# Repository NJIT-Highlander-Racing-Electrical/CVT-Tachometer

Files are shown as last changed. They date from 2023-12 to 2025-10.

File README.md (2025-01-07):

 # CVT-Tachometer

A subsystem that measures the RPM of the primary and secondary on the CVT. This subsystem also has a temperature sensor to detect if the CVT is overheating.

## 2024-2025 Design Goals

* Everything last year seemed to work well, but a few improvements to the existing system could be made:
  * Software
       * Improve program to do more analog reads and spend less time processing data
          * This may involve constants that are only calculated once during setup, faster math functions, fewer delays, etc
       * Use the analog reads for IR sensors on both ADC1 and ADC2 to prevent any issues. 
  * Sensor Enclosures
       * the sensor housings should be made out of something other than PLA
       * they should be able to fit custom PCBs with connectors
       * the hood around the emitter and receiver should be enlarged to prevent anything else from reflecting other than what is directly in front
  * PCBs for sensors
       * the wiring from the sensors to the main electronics housing were tough to do
       * A small PCB for the electronics would be nicer than hand soldering wires
       * A connector would also be good so that they can be removed/swapped easily
            * Maybe 1x4 or 1x5 or 1x6 JST depending on how many conductors we need going to each board
  * Additional TMP36 Sensor
      * Another TMP36 temperature sensor can be added so that there is only one version of the sensor PCB, and we get a better idea of the temperature gradient within the CVT case (primary vs secondary).
  * Additional Note
     * On the IR receiver output, have it split to two GPIO. One leg has a potentiometer (0-10k?) between the output and the GPIO for finding the optimal resistance. Also make sure it has a small series resistor to prevent resistance from dropping completely to zero. The other GPIO has a fixed resistor that can be added after the fact that will be used in the long term. 

## Hardware Components:

* IR Sensors that point at primary and secondary.
- These can detect when a white stripe on the CVT passes by (one revolution)
* Microcontroller to convert the number of revolutions per second into an RPM value for dashboard and DAS (via CAN-Bus)
  - Uses ESP32 and TJA1051T CAN-Bus transceiver
* TMP36 Temperature Sensor to look at ambient temperature in the CVT case
- Sends a bit via CAN-Bus to turn on an overheating status LED on the dashboard

 ## Notes

 * Super-Bright IR LEDs support an output current of 100mA with a forward voltage of 1.6V. This means a voltage drop of 5V-1.6V = 3.4V across the 1W resistor. To achieve a current of roughly 75mA, we are using a 47 ohm resistor
    * 5V -> IR LED -> Resistor -> Ground
 * Using standard infrared photodiodes, we can simply power the IR leds without needing a 38kHz pulse rate
    * 5V -> IR Diode -> Resistor -> Ground (sample signal between diode and resistor voltage divider)
 * Temperature sensor is TMP36
    * 5V - > TMP36 VCC, GND -> TMP 36 GND, VOUT -> GPIO
 * Connections from the LEDs/sensors to the main body should be sealed/waterproof
 * The holes in the CVT case should be 20mm
 * The infrared diode appears to act like a variable resistor, but voltage polarity must be + on cathode (short negative leg) and - on anode (short positive leg)

 * The software utilizes the dual core functionality of the ESP32
   * Core 1 reads primaryRPM and deals with CAN-Bus communication
      * It is very important that all other processing is kept to a minimum to ensure primaryRPM is accurately read
   * Core 0 solely reads secondaryRPM

### Previous Issues 
 * One issue noticed during the testing phase was that the analog sensor readings were constantly peaking (4095). The resistor divider for the IR receivers needed to be adjusted to roughly 2700 ohms
 * It looked like the analog readings were having issues at comp too. It was either 0-3 ish mph or 41
     * This has been solved on 9/18/24 with dynamically adjusting analog thresholds
 * Analog reads are not ideal for this type of data acquisition. Fast readings are needed, and there should be no margin for error about whether a reading falls within a range
 * Digital readings with a hall sensor, engine spark plug with octocoupler, or some other digital signal could be implemented 

## Electrical Wiring Notes

### Pins to sensor modules

* Pin 1: +5V
* Pin 2: GND
* Pin 3: TMP36 Output
* Pin 4: IR Emitter Return Line
* Pin 5: IR Receiver Return Line

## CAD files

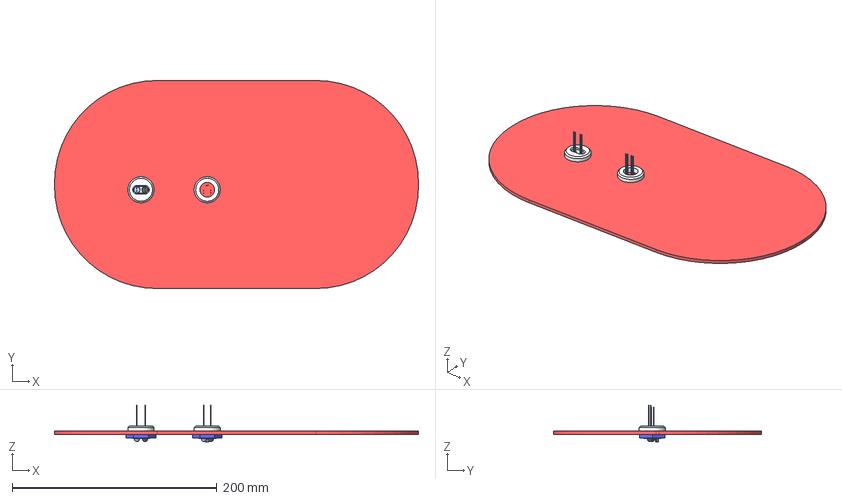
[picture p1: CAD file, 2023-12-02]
3D Models/CVT Infrared Sensors Full Model.step
355.6 x 203.2 x 35.7 mm
5mm LED v1 x 2
5mm LED v1 (1) x 2
TO92 Transistor TMP36 Temperature Sensor Package

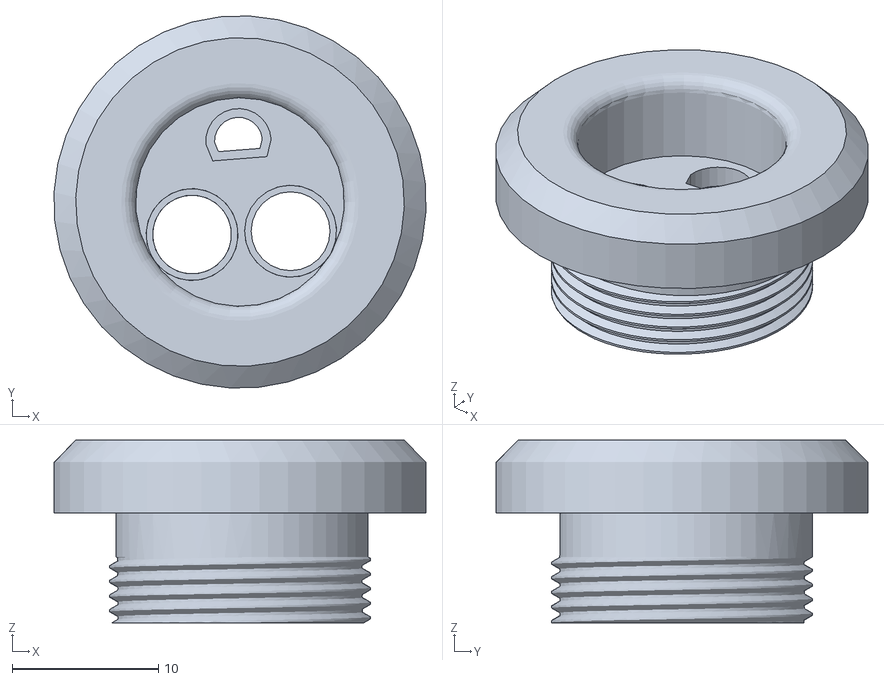
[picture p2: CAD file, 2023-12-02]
3D Models/CVT Infrared Sensors Main Body (With Temperature Sensor).stl
25.5 x 25.5 x 12.5

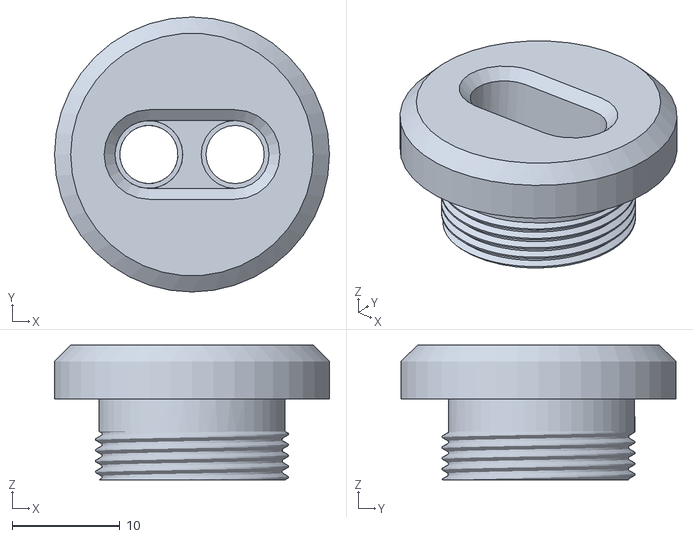
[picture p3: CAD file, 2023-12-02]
3D Models/CVT Infrared Sensors Main Body (No Temperature Sensor).stl
25.5 x 25.5 x 12.5

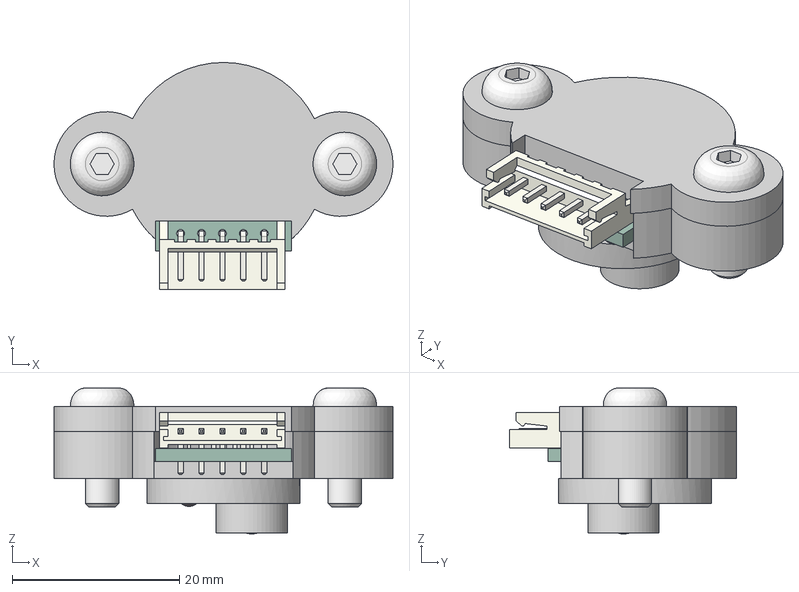
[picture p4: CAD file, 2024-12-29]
3D Models/CVT Sensor Module Enclosures v5.step
40.5 x 27.1 x 17.4 mm
JST_S5B_EH
LED_D3.0mm_IRBlack_1
TO-92_Inline_Narrow
LED_D5.0mm_IRGrey_1
SensorPCB_PCB
VITE_TESTA_BOMBATA_ESAGONO_INCASSATO x 2

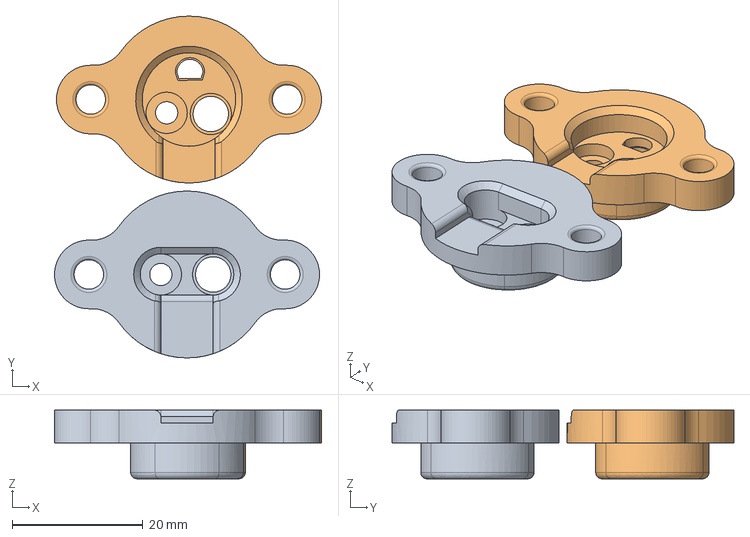
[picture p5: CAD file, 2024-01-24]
3D Models/CVT Infrared Sensor Mounts.step
40.8 x 52.2 x 10.5 mm

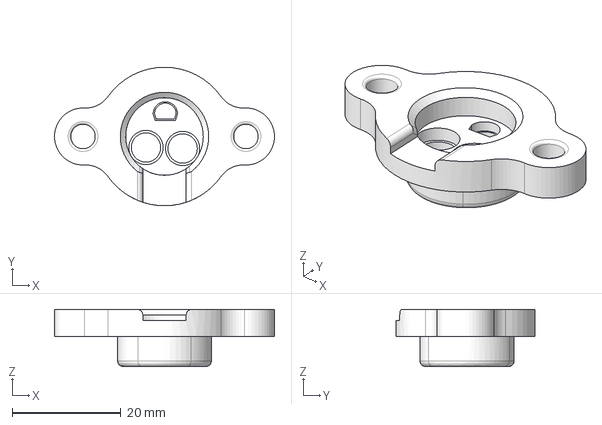
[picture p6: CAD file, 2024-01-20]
3D Models/Sensor Mount with Temperature.step
40.5 x 25.5 x 10.5 mm

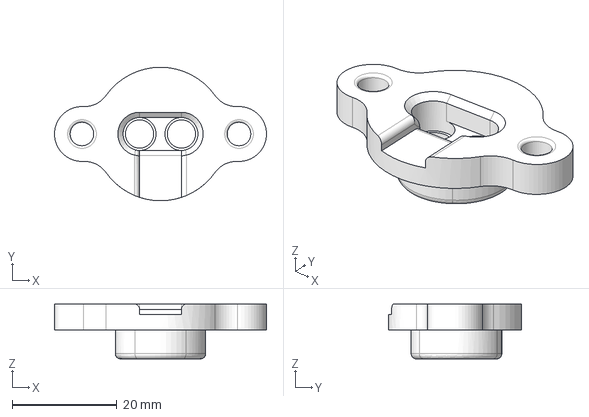
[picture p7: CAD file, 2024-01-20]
3D Models/Sensor Mount No Temperature.step
40.5 x 25.5 x 10.5 mm

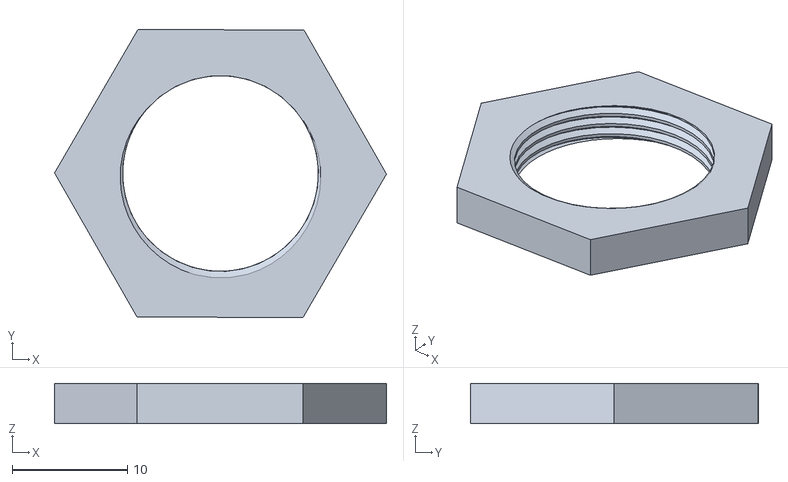
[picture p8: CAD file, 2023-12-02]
3D Models/CVT Infrared Sensors Nut.stl
28.9 x 25.0 x 3.50

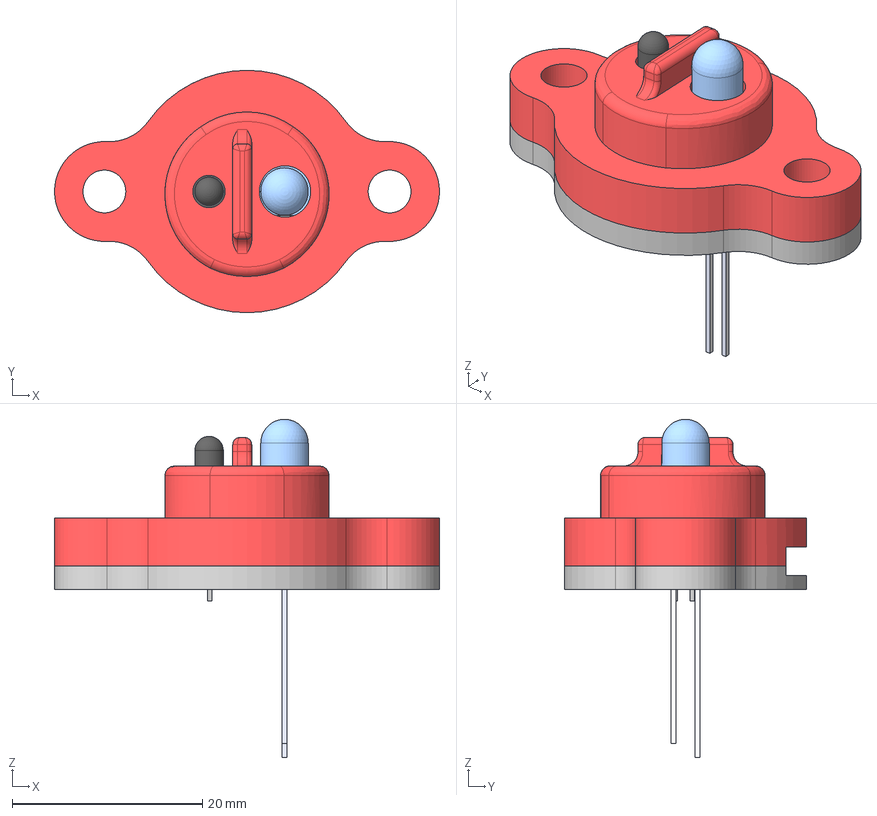
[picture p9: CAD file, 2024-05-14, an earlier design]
2023-2024 Archive/3D Models/CVT Infrared Sensor (no temperature).step
40.5 x 25.5 x 35.6 mm
5mm LED v1
led_energy
led_pin.1.1.1
led_pin.2.1

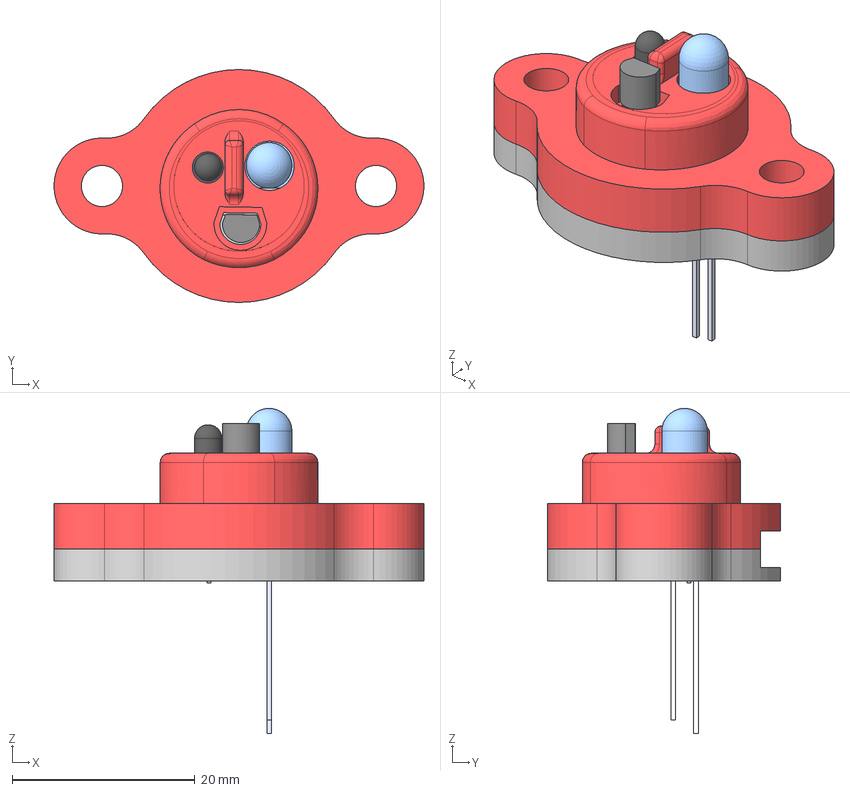
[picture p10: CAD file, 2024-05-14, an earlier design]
2023-2024 Archive/3D Models/CVT Infrared Sensors (with temperature).step
40.5 x 25.5 x 35.6 mm
TO92 Transistor TMP36 Temperature Sensor Package
5mm LED v1
led_energy
led_pin.1.1.1
led_pin.2.1

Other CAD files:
3D Models/Alternative Designs/CVTMain v2.step
2023-2024 Archive/3D Models/OldDesigns/CVT Infrared Sensors Full Model.step
2023-2024 Archive/3D Models/OldDesigns/Sensor Mount No Temperature.step
2023-2024 Archive/3D Models/OldDesigns/Sensor Mount with Temperature.step
2023-2024 Archive/3D Models/OldDesigns/CVT Infrared Sensor Mounts.step
3D Models/CVT Sensor Module Enclosures.f3z

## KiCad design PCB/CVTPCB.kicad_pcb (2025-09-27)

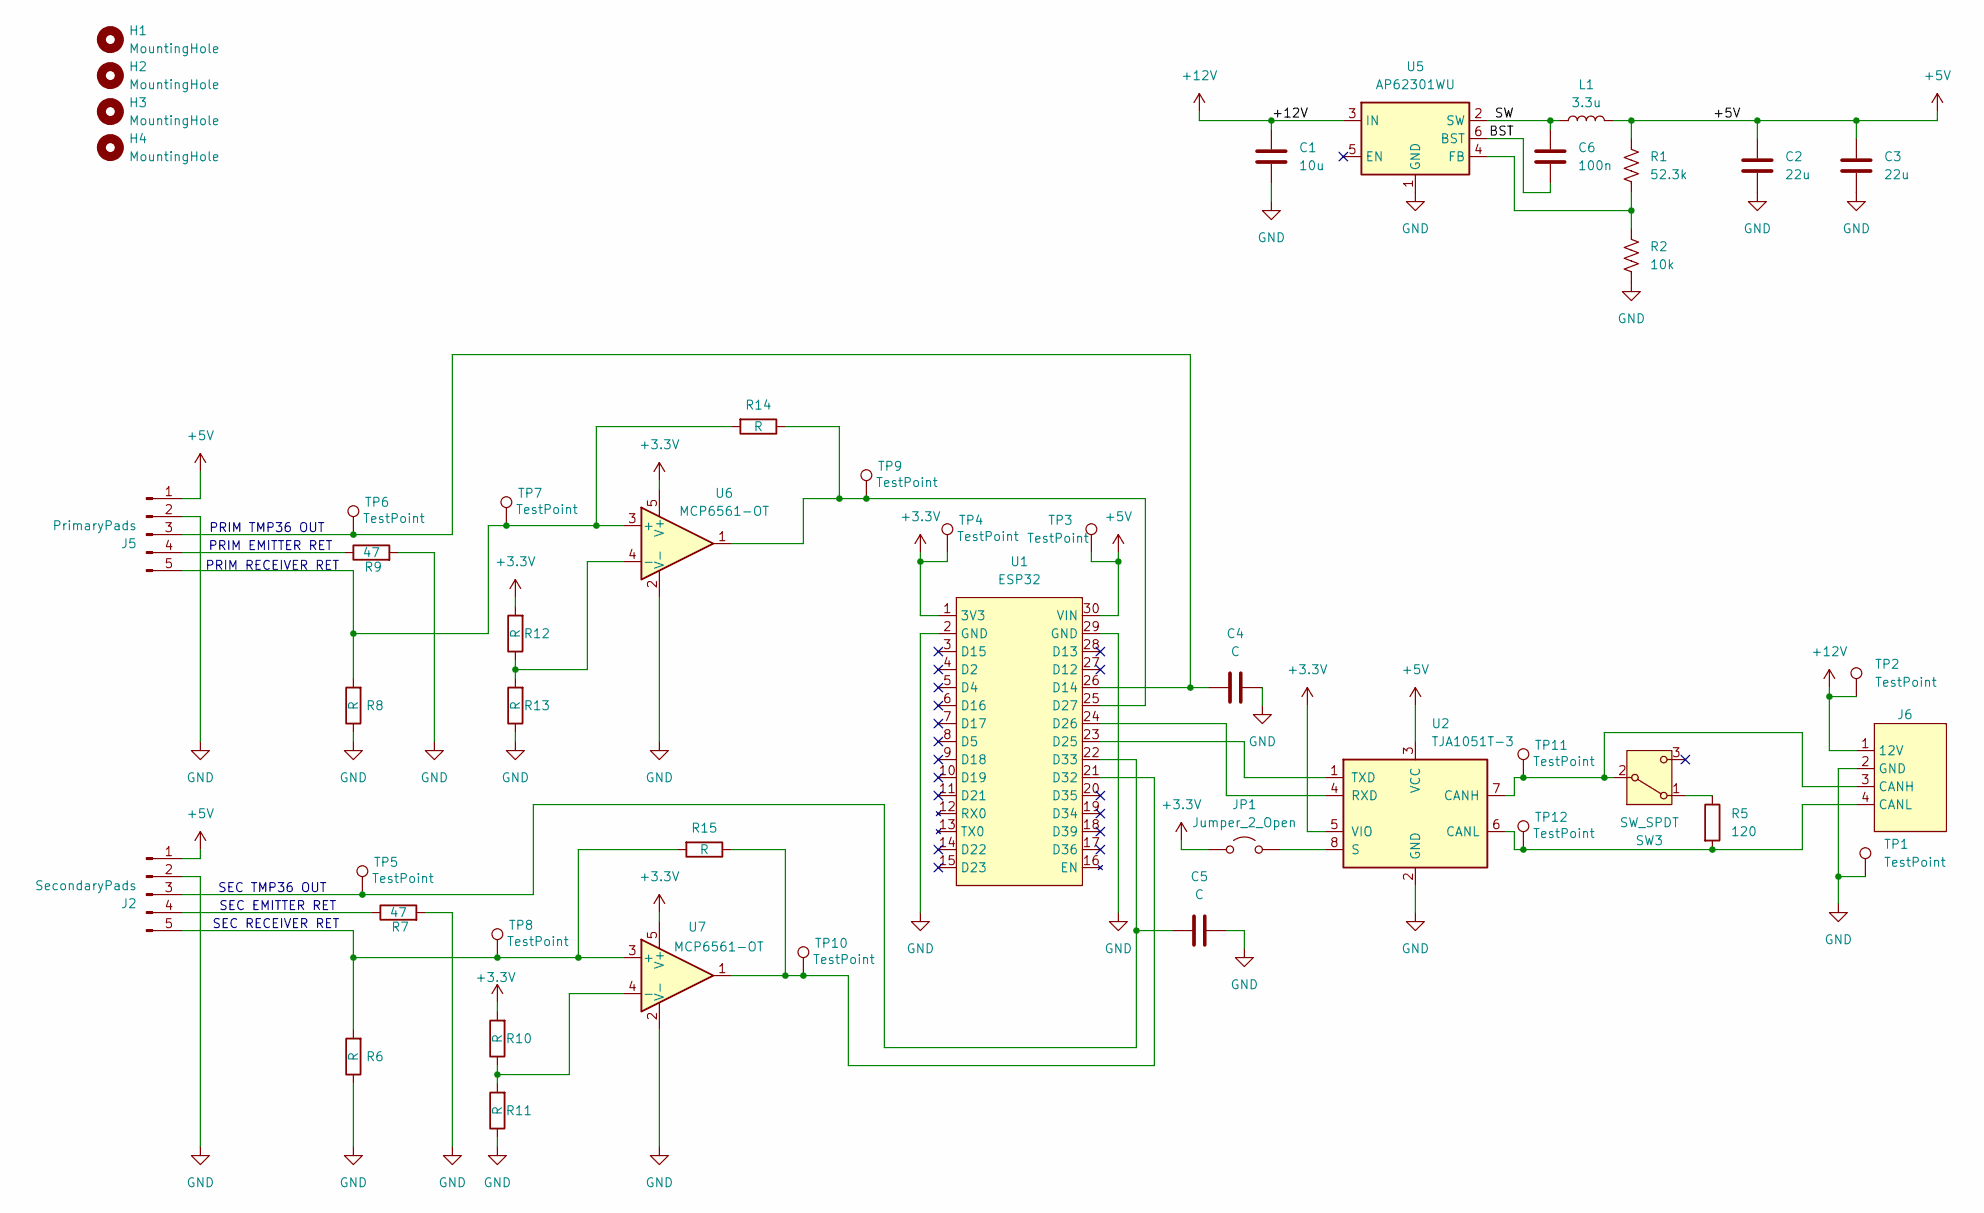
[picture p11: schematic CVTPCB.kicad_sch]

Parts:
C1: 10u; C_0805_2012Metric_Pad1.18x1.45mm_HandSolder
C2, C3: 22u; C_0603_1608Metric_Pad1.08x0.95mm_HandSolder
C4, C5: C; C_0805_2012Metric_Pad1.18x1.45mm_HandSolder
C6: 100n; C_0402_1005Metric_Pad0.74x0.62mm_HandSolder
H1, H2, H3, H4: MountingHole; MountingHole_4.3mm_M4
J2: SecondaryPads; Temp_IR_5_Pad_Combo
J5: PrimaryPads; Temp_IR_5_Pad_Combo
J6: Aviation Plug Pads
JP1: Jumper_2_Open; SolderJumper-2_P1.3mm_Open_Pad1.0x1.5mm
L1: 3.3u; L_Taiyo-Yuden_NR-50xx
R1: 52.3k; R_0402_1005Metric
R2: 10k; R_0402_1005Metric
R5: 120; R_1206_3216Metric_Pad1.30x1.75mm_HandSolder
R6, R8, R10, R11, R12, R13, R14, R15: R; R_1206_3216Metric_Pad1.30x1.75mm_HandSolder
R7, R9: 47; R_Axial_DIN0411_L9.9mm_D3.6mm_P12.70mm_Horizontal
SW3: SW_SPDT; SW_SPDT_CK_JS102011SAQN
TP1, TP2, TP3, TP4, TP5, TP6, TP7, TP8, TP9, TP10, TP11, TP12: TestPoint; TestPoint_THTPad_D3.0mm_Drill1.5mm
U1: ESP32
U2: TJA1051T-3; SOIC-8_3.9x4.9mm_P1.27mm
U5: AP62301WU; TSOT-23-6
U6, U7: MCP6561-OT; SOT-23-5

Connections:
+3.3V: JP1.1 (A), R10.2, R12.2, TP4.1, U1.1 (3V3), U2.5 (VIO), U6.5 (V+), U7.5 (V+)
+5V: C2.1, C3.1, J2.1, J5.1, L1.2, R1.1, TP3.1, U1.30 (VIN), U2.3 (VCC)
+12V: C1.1, J6.1 (12V), TP2.1, U5.3 (IN)
/BST: C6.2, U5.6 (BST)
/SW: C6.1, L1.1, U5.2 (SW)
GND: C1.2, C2.2, C3.2, C4.2, C5.2, J2.2, J5.2, J6.2 (GND), R2.2, R6.1, R7.2, R8.1, R9.2, R11.1, R13.1, TP1.1, U1.2 (GND), U1.29 (GND), U2.2 (GND), U5.1 (GND), U6.2 (V-), U7.2 (V-)
unnamed: C5.1, J2.3, TP5.1, U1.22 (D33)
unnamed: J2.4, R7.1
unnamed: J2.5, R6.2, R15.2, TP8.1, U7.3 (+)
unnamed: C4.1, J5.3, TP6.1, U1.26 (D14)
unnamed: J5.4, R9.1
unnamed: J5.5, R8.2, R14.2, TP7.1, U6.3 (+)
unnamed: J6.3 (CANH), SW3.2 (B), TP11.1, U2.7 (CANH)
unnamed: J6.4 (CANL), R5.2, TP12.1, U2.6 (CANL)
unnamed: JP1.2 (B), U2.8 (S)
unnamed: R5.1, SW3.1 (A)
unnamed: U1.23 (D25), U2.1 (TXD)
unnamed: U1.24 (D26), U2.4 (RXD)
unnamed: R14.1, TP9.1, U1.25 (D27), U6.1
unnamed: R15.1, TP10.1, U1.21 (D32), U7.1
unnamed: R1.2, R2.1, U5.4 (FB)
unnamed: R12.1, R13.2, U6.4 (-)
unnamed: R10.1, R11.2, U7.4 (-)

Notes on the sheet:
PRIM TMP36 OUT
SEC RECEIVER RET
SEC EMITTER RET
PRIM EMITTER RET
PRIM RECEIVER RET
SEC TMP36 OUT

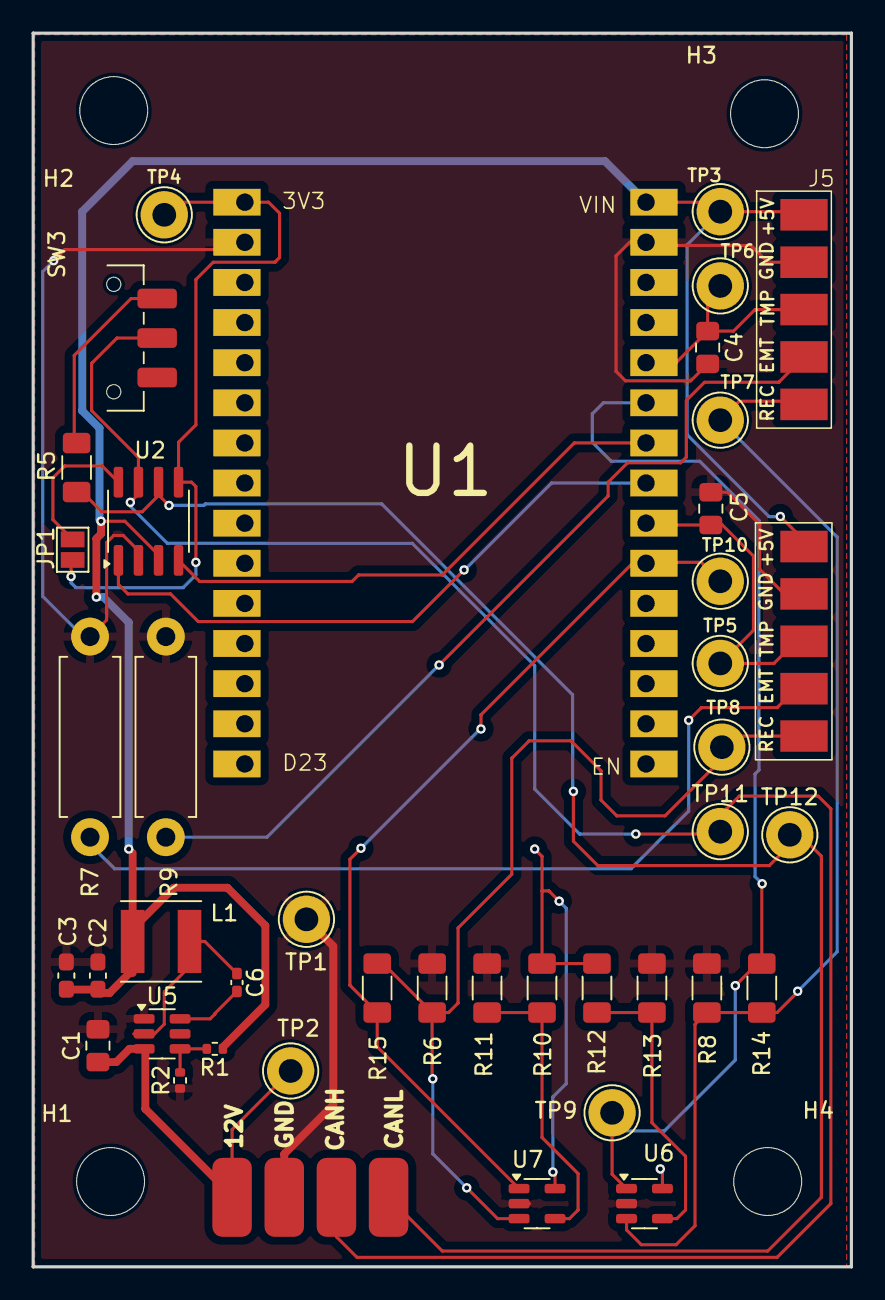
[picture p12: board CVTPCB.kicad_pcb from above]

Board: 2 copper layers, 51.8 x 78.1 mm, 46 parts (0 on the bottom side), 23 nets.

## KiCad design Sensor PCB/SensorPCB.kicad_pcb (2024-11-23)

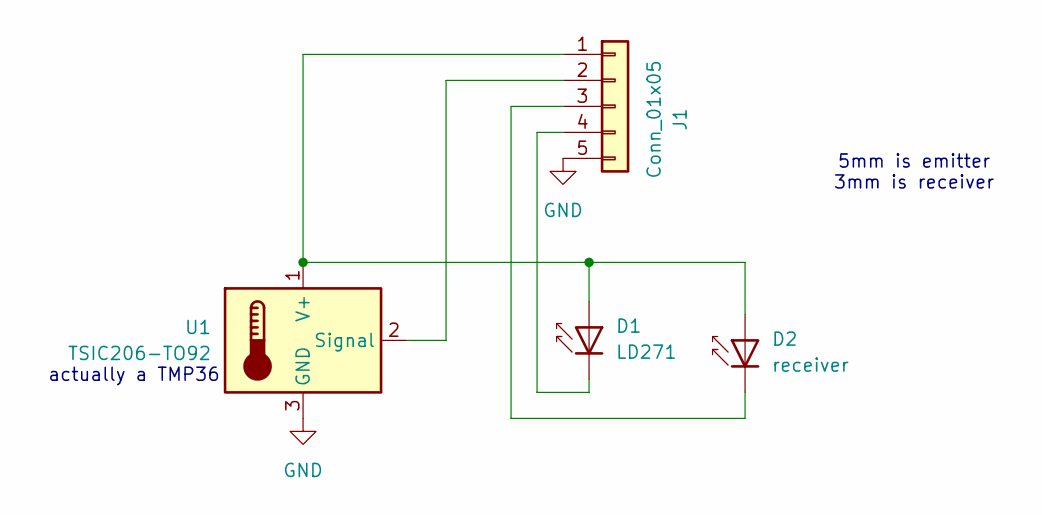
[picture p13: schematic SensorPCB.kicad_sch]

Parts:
D1: LD271; LED_D5.0mm_IRGrey
D2: receiver; LED_D3.0mm_IRBlack
J1: Conn_01x05; JST_EH_B5B-EH-A_1x05_P2.50mm_Vertical
U1: TSIC206-TO92; TO-92_Inline

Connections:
GND: J1.5, U1.3 (GND)
unnamed: D1.2 (A), D2.2 (A), J1.1, U1.1 (V+)
unnamed: D1.1 (K), J1.4
unnamed: D2.1 (K), J1.3
unnamed: J1.2, U1.2 (Signal)

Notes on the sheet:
5mm is emitter 3mm is receiver
actually a TMP36

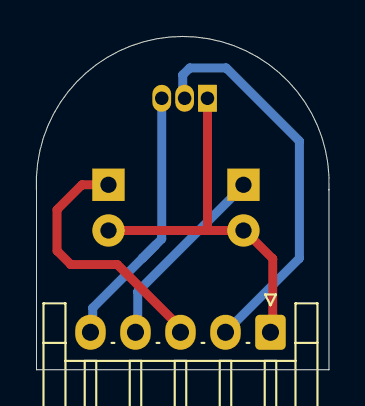
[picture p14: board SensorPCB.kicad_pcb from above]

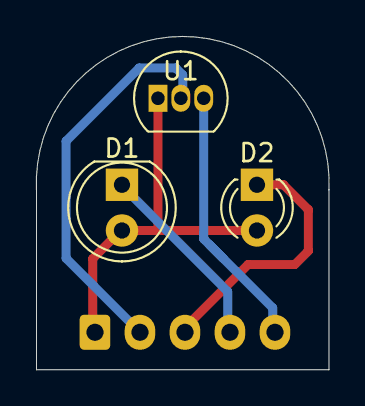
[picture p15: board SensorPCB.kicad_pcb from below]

Board: 2 copper layers, 16.3 x 18.5 mm, 4 parts (3 on the bottom side), 5 nets.

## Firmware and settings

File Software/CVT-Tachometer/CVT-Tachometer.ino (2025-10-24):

/*
* CVT Tachometer with IR sensors and temperature monitoring
* Fixed timing issues, race conditions, and improved filtering
*/

#include "BajaCAN.h"
#include <Wire.h>

// Set DEBUG to false for final program
#define DEBUG true

#define DEBUG_SERIAL \
  if (DEBUG) Serial

#define PRIMARY_IR 32    // Primary Comparator Output
#define PRIMARY_TEMP 33  // Primary TMP36 Sensor pin

#define SECONDARY_IR 27    // Secondary Comparator Output
#define SECONDARY_TEMP 14  // Secondary TMP36 Sensor pin

// MLX90614 I2C Configuration
#define MLX90614_I2C_ADDR 0x5A
#define MLX90614_OBJECT_TEMP 0x07
#define I2C_SDA 21
#define I2C_SCL 22

// USER-DEFINED PARAMETERS
const int debugPrintInterval = 100;
const int tempUpdateFrequency = 500;
const int numPrimaryTargets = 8;
const int numSecondaryTargets = 3;

// Timeout if no pulse in 1 second (1,000,000 microseconds)
const unsigned long timeoutThreshold = 1000000;

// Debounce time - adjusted for realistic RPM ranges
// Primary: 8 targets, max ~4000 RPM = 533 pulses/sec = 1875us between pulses
// Secondary: 3 targets, max ~4000 RPM = 200 pulses/sec = 5000us between pulses
// Set debounce to 1500us to allow fast speeds while rejecting noise
const unsigned long debounceTimeMicros = 1500;

// Maximum reasonable RPM to filter out noise spikes
const int MAX_PRIMARY_RPM = 5000;
const int MAX_SECONDARY_RPM = 5000;

// END USER PARAMETERS

// Serial Print timing
int lastPrintTime = 0;

// Primary timing variables (all volatile for ISR safety)
volatile unsigned long currentPrimaryReadTime = 0;
volatile unsigned long lastPrimaryReadTime = 0;
volatile bool primaryUpdateFlag = false;

// Secondary timing variables
volatile unsigned long currentSecondaryReadTime = 0;
volatile unsigned long lastSecondaryReadTime = 0;
volatile bool secondaryUpdateFlag = false;

// Temperature timing
unsigned long lastPrimTempReadTime = 0;
unsigned long lastSecTempReadTime = 0;
unsigned long lastBeltTempReadTime = 0;

// State flags
bool primaryIsFirstReading = true;
bool secondaryIsFirstReading = true;
bool primaryIgnoreNext = false;
bool secondaryIgnoreNext = false;

// Moving average filter (median filter for better spike rejection)
const int RPM_FILTER_SIZE = 5;
int primaryRPMBuffer[RPM_FILTER_SIZE] = {0};
int secondaryRPMBuffer[RPM_FILTER_SIZE] = {0};
int primaryBufferIndex = 0;
int secondaryBufferIndex = 0;
int primaryBufferCount = 0;  // Track how many samples we have
int secondaryBufferCount = 0;

// Function Prototypes
void primaryISR();
void secondaryISR();
void readPrimaryTemp();
void readSecondaryTemp();
void readBeltTemp();
void checkPrimaryTimeout();
void checkSecondaryTimeout();
int calculateMedianRPM(int* buffer, int size);
void printData();

void setup() {
  Serial.begin(460800);
  delay(100);

  // Initialize I2C for MLX90614
  Wire.begin(I2C_SDA, I2C_SCL);
  
  // Initialize CAN - send every 25ms (40Hz)
  setupCAN(CVT, 25);

  // Configure pins
  pinMode(PRIMARY_IR, INPUT);
  pinMode(PRIMARY_TEMP, INPUT);
  pinMode(SECONDARY_IR, INPUT);
  pinMode(SECONDARY_TEMP, INPUT);

  // Initialize timing to current time
  unsigned long now = micros();
  currentPrimaryReadTime = now;
  lastPrimaryReadTime = now;
  currentSecondaryReadTime = now;
  lastSecondaryReadTime = now;

  // Attach interrupts on rising edge
  attachInterrupt(digitalPinToInterrupt(PRIMARY_IR), primaryISR, RISING);
  attachInterrupt(digitalPinToInterrupt(SECONDARY_IR), secondaryISR, RISING);

  DEBUG_SERIAL.println("CVT Tachometer Initialized");
  DEBUG_SERIAL.print("Primary targets: ");
  DEBUG_SERIAL.println(numPrimaryTargets);
  DEBUG_SERIAL.print("Secondary targets: ");
  DEBUG_SERIAL.println(numSecondaryTargets);
  DEBUG_SERIAL.print("Debounce time (us): ");
  DEBUG_SERIAL.println(debounceTimeMicros);
}

void loop() {
  // Check for timeouts
  checkPrimaryTimeout();
  checkSecondaryTimeout();

  // Process primary RPM calculation
  if (primaryUpdateFlag) {
    // Capture timing atomically
    noInterrupts();
    unsigned long capturedCurrent = currentPrimaryReadTime;
    unsigned long capturedLast = lastPrimaryReadTime;
    primaryUpdateFlag = false;
    interrupts();

    // Skip first reading - need two points to calculate
    if (primaryIsFirstReading) {
      noInterrupts();
      lastPrimaryReadTime = capturedCurrent;
      interrupts();
      primaryIsFirstReading = false;
      primaryIgnoreNext = false;
      DEBUG_SERIAL.println("Primary: First reading captured");
    }
    // If recovering from timeout, re-establish baseline
    else if (primaryIgnoreNext) {
      noInterrupts();
      lastPrimaryReadTime = capturedCurrent;
      interrupts();
      primaryIgnoreNext = false;
      DEBUG_SERIAL.println("Primary: Baseline re-established after timeout");
    }
    // Normal calculation
    else {
      unsigned long elapsed = capturedCurrent - capturedLast;
      
      if (elapsed > 0) {
        // Calculate RPM: (60,000,000 microseconds/min) / elapsed / targets
        int calculatedRPM = (60000000.0 / elapsed) / numPrimaryTargets;

        // Sanity check
        if (calculatedRPM > 0 && calculatedRPM < MAX_PRIMARY_RPM) {
          // Add to buffer
          primaryRPMBuffer[primaryBufferIndex] = calculatedRPM;
          primaryBufferIndex = (primaryBufferIndex + 1) % RPM_FILTER_SIZE;
          if (primaryBufferCount < RPM_FILTER_SIZE) {
            primaryBufferCount++;
          }
          
          // Calculate filtered value
          primaryRPM = calculateMedianRPM(primaryRPMBuffer, primaryBufferCount);
          
          // Update last reading time atomically
          noInterrupts();
          lastPrimaryReadTime = capturedCurrent;
          interrupts();
        } else {
          DEBUG_SERIAL.print("Primary RPM rejected: ");
          DEBUG_SERIAL.println(calculatedRPM);
        }
      }
    }
  }

  // Process secondary RPM calculation
  if (secondaryUpdateFlag) {
    // Capture timing atomically
    noInterrupts();
    unsigned long capturedCurrent = currentSecondaryReadTime;
    unsigned long capturedLast = lastSecondaryReadTime;
    secondaryUpdateFlag = false;
    interrupts();

    // Skip first reading - need two points to calculate
    if (secondaryIsFirstReading) {
      noInterrupts();
      lastSecondaryReadTime = capturedCurrent;
      interrupts();
      secondaryIsFirstReading = false;
      secondaryIgnoreNext = false;
      DEBUG_SERIAL.println("Secondary: First reading captured");
    }
    // If recovering from timeout, re-establish baseline
    else if (secondaryIgnoreNext) {
      noInterrupts();
      lastSecondaryReadTime = capturedCurrent;
      interrupts();
      secondaryIgnoreNext = false;
      DEBUG_SERIAL.println("Secondary: Baseline re-established after timeout");
    }
    // Normal calculation
    else {
      unsigned long elapsed = capturedCurrent - capturedLast;
      
      if (elapsed > 0) {
        // Calculate RPM
        int calculatedRPM = (60000000.0 / elapsed) / numSecondaryTargets;

        // Sanity check
        if (calculatedRPM > 0 && calculatedRPM < MAX_SECONDARY_RPM) {
          // Add to buffer
          secondaryRPMBuffer[secondaryBufferIndex] = calculatedRPM;
          secondaryBufferIndex = (secondaryBufferIndex + 1) % RPM_FILTER_SIZE;
          if (secondaryBufferCount < RPM_FILTER_SIZE) {
            secondaryBufferCount++;
          }
          
          // Calculate filtered value
          secondaryRPM = calculateMedianRPM(secondaryRPMBuffer, secondaryBufferCount);
          
          // Update last reading time atomically
          noInterrupts();
          lastSecondaryReadTime = capturedCurrent;
          interrupts();
        } else {
          DEBUG_SERIAL.print("Secondary RPM rejected: ");
          DEBUG_SERIAL.println(calculatedRPM);
        }
      }
    }
  }

  // Read temperatures
  readPrimaryTemp();
  readSecondaryTemp();
  readBeltTemp();

  // Print debug data
  if (DEBUG && (millis() - lastPrintTime) > debugPrintInterval) {
    lastPrintTime = millis();
    printData();
  }
}

/*
 * FUNCTION DEFINITIONS
 */

void primaryISR() {
  unsigned long now = micros();
  
  // Debounce: ignore pulses too close together
  unsigned long timeSinceLast = now - currentPrimaryReadTime;
  if (timeSinceLast < debounceTimeMicros) {
    return;  // Noise/bounce, ignore
  }
  
  // Update timing
  lastPrimaryReadTime = currentPrimaryReadTime;
  currentPrimaryReadTime = now;
  primaryUpdateFlag = true;
}

void secondaryISR() {
  unsigned long now = micros();
  
  // Debounce: ignore pulses too close together
  unsigned long timeSinceLast = now - currentSecondaryReadTime;
  if (timeSinceLast < debounceTimeMicros) {
    return;  // Noise/bounce, ignore
  }
  
  // Update timing
  lastSecondaryReadTime = currentSecondaryReadTime;
  currentSecondaryReadTime = now;
  secondaryUpdateFlag = true;
}

void checkPrimaryTimeout() {
  unsigned long currentTime = micros();
  unsigned long timeSinceLastPulse = currentTime - currentPrimaryReadTime;
  
  if (timeSinceLastPulse > timeoutThreshold) {
    if (primaryRPM != 0) {  // Only update if not already zero
      primaryRPM = 0;
      primaryIgnoreNext = true;  // Ignore next pulse to re-establish baseline
      
      // Clear the buffer
      for (int i = 0; i < RPM_FILTER_SIZE; i++) {
        primaryRPMBuffer[i] = 0;
      }
      primaryBufferCount = 0;
      primaryBufferIndex = 0;
      
      DEBUG_SERIAL.println("Primary timeout - RPM set to 0");
    }
  }
}

void checkSecondaryTimeout() {
  unsigned long currentTime = micros();
  unsigned long timeSinceLastPulse = currentTime - currentSecondaryReadTime;
  
  if (timeSinceLastPulse > timeoutThreshold) {
    if (secondaryRPM != 0) {  // Only update if not already zero
      secondaryRPM = 0;
      secondaryIgnoreNext = true;  // Ignore next pulse to re-establish baseline
      
      // Clear the buffer
      for (int i = 0; i < RPM_FILTER_SIZE; i++) {
        secondaryRPMBuffer[i] = 0;
      }
      secondaryBufferCount = 0;
      secondaryBufferIndex = 0;
      
      DEBUG_SERIAL.println("Secondary timeout - RPM set to 0");
    }
  }
}

int calculateMedianRPM(int* buffer, int count) {
  if (count == 0) return 0;
  
  // Create temporary array for sorting
  int sortedBuffer[RPM_FILTER_SIZE];
  memcpy(sortedBuffer, buffer, count * sizeof(int));
  
  // Bubble sort
  for (int i = 0; i < count - 1; i++) {
    for (int j = 0; j < count - i - 1; j++) {
      if (sortedBuffer[j] > sortedBuffer[j + 1]) {
        int temp = sortedBuffer[j];
        sortedBuffer[j] = sortedBuffer[j + 1];
        sortedBuffer[j + 1] = temp;
      }
    }
  }
  
  // Return median value
  return sortedBuffer[count / 2];
}

void readPrimaryTemp() {
  if ((millis() - lastPrimTempReadTime) > tempUpdateFrequency) {
    long total = 0;

    // Average 10 readings
    for (int i = 0; i < 10; i++) {
      total += analogRead(PRIMARY_TEMP);
    }

    int primTempReading = total / 10;
    float primTempVoltage = (float)primTempReading * 3.3 / 4095.0;
    float primTempC = (primTempVoltage - 0.5) * 100;
    primaryTemperature = (primTempC * 9.0 / 5.0) + 32.0;

    lastPrimTempReadTime = millis();
  }
}

void readSecondaryTemp() {
  if ((millis() - lastSecTempReadTime) > tempUpdateFrequency) {
    long total = 0;

    // Average 10 readings
    for (int i = 0; i < 10; i++) {
      total += analogRead(SECONDARY_TEMP);
    }

    int secTempReading = total / 10;
    float secTempVoltage = (float)secTempReading * 3.3 / 4095.0;
    float secTempC = (secTempVoltage - 0.5) * 100;
    secondaryTemperature = (secTempC * 9.0 / 5.0) + 32.0;

    lastSecTempReadTime = millis();
  }
}

void readBeltTemp() {
  if ((millis() - lastBeltTempReadTime) > tempUpdateFrequency) {
    Wire.beginTransmission(MLX90614_I2C_ADDR);
    Wire.write(MLX90614_OBJECT_TEMP);
    
    if (Wire.endTransmission(false) == 0) {
      Wire.requestFrom(MLX90614_I2C_ADDR, 3);
      
      if (Wire.available() >= 2) {
        uint8_t tempLow = Wire.read();
        uint8_t tempHigh = Wire.read();
        Wire.read(); // Discard PEC byte
        
        uint16_t tempRaw = (tempHigh << 8) | tempLow;
        float tempK = tempRaw * 0.02;
        float tempC = tempK - 273.15;
        float tempF = (tempC * 9.0 / 5.0) + 32.0;
        
        beltTemperature = (int)tempF;
      }
    }
    
    lastBeltTempReadTime = millis();
  }
}

void printData() {
  DEBUG_SERIAL.print("pRpm:");
  DEBUG_SERIAL.print(primaryRPM);
  DEBUG_SERIAL.print(", pTemp:");
  DEBUG_SERIAL.print(primaryTemperature);
  DEBUG_SERIAL.print(", sRpm:");
  DEBUG_SERIAL.print(secondaryRPM);
  DEBUG_SERIAL.print(", sTemp:");
  DEBUG_SERIAL.print(secondaryTemperature);
  DEBUG_SERIAL.print(", beltTemp:");
  DEBUG_SERIAL.println(beltTemperature);
}

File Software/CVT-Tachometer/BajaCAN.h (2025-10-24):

/*********************************************************************************
*
*   BajaCAN.h  -- Version 2.2.2 - Native ESP32 CAN Driver
*
*   The goal of this BajaCAN header/driver is to enable all subsystems throughout
*   the vehicle to use the same variables, data types, and functions. That way,
*   any changes made to the CAN bus system can easily be applied to each subsystem
*   by simply updating the version of this file.

*
*     This driver serves several functions:
*

*     *** CAN Setup/Initialization ***
*
*     This CAN driver declares all of the variables that will be used in
*     CAN transmissions. That way, there is no confusion as to what data packet
*     a variable name refers to. In addition, declaring the variables in the CAN
*     header file allows for each variable to have the same data type. If one
*     subsystem were to use a float for an RPM value while another uses an integer,
*     there is a chance we could run into issues.
*
*     Before using CAN, several initialization steps must be taken. Since this must
*     happen during the setup() of the main code, there is a function named
*     setupCAN() that can be called in the setup() portion to execute all CAN setup.
*     Ideally, all subsystems will use the same pair of GPIO for CAN that do not
*     have any special functions. However, if setup does differ between subsystems,
*     setupCAN() has optional arguments for baud rate, GPIO, send frequency, etc.
*     The only argument that must be passed into setupCAN is a subsystem name
*     (e.g. DASHBOARD) which is used to determine which CAN messages should be
*     transmitted from each subsystem.
*
*     A pinout for the ESP32's we use can be found here:
*     https://lastminuteengineers.com/wp-content/uploads/iot/ESP32-Pinout.png
*
*     While most pins can technically be used for CAN, some should be avoided.
*     - GPIO0, GPIO2, GPIO5, GPIO12, and GPIO15 are strapping pins used during boot
*     - GPIO34, GPIO35, GPIO36, and GPIO39 are input-only pins
*     - GPIO5, GPIO18, GPIO19, and GPIO23 are used for SPI
*     - GPIO21 and GPIO22 are used for I2C
*     - GPIO1 and GPIO3 are used for Serial communication with a PC
*
*     Also in CAN setup, we must configure the data rate to be used. This can be
*     50Kbps, 80Kbps, 100Kbps, etc. We will generally use 500Kbps as it provides a
*     sufficiently high data rate which also being slow enough to make signal issues
*     less common. Note that newer ESP32 microcontrollers have an issue in their CAN
*     hardware that causes them to run at half of the provided data rate. Therefore,
*     most of our subsytems should be configured at 1000Kbps.
*
*
*
*     *** CAN Receiving ***
*
*     This part of the driver is responsible for parsing incoming packets, getting the
*     packet ID, and then sorting the receiving data into the proper variable. For
*     simplicity purposes, each subsystem sorts all valid data transmissions it
*     receives, even if that data packet isn't pertient to its function. Hardware
*     limitations should not be an issue, as CAN has its own dedicated core for
*     processing on each subsystem. The ESP32 also has plenty of memory to store all of
*     the data packets we use in CAN transmission.
*
*     When the program needs to work with a variable, such as updating a display or
*     saving data to an SD card, it can simply pass the variable knowing the CAN
*     driver has updated it with the newest value.
*
*
*
*     *** CAN Sending ***
*
*     This driver categorizes each variable based off of which subsystem should be
*     sending it. By passing through a subsystem name in setupCAN(), the subsybstem is
*     essentially telling the CAN driver, "Hey, I'm the CVT." Then, the driver would know
*     to only send CAN packets that the CVT should be updating with new data. Something
*     like the dashboard should never be reporting an RPM value to the rest of the vehicle
*     since it's not obtaining that data. This makes writing the main code easier, as CAN
*     data can just be sent on a fixed interval without any intervention by the main code.
*
*
*     *** Roadmap Ideas ***
*       - Implement a flag that is set when a data value is updated, and reset when
*         the main core reads that new data value. This could be practical in
*         situations where we need to be sure that the data we're using is recent.
*         There could even be a flag received from the main code that the CAN driver
*         uses to know when it has data to send out
*
*
************************************************************************************/

#include "driver/can.h"

// CAN Configuration
#define CAN_BAUD_RATE CAN_TIMING_CONFIG_500KBITS()
#define CAN_TX_GPIO GPIO_NUM_25
#define CAN_RX_GPIO GPIO_NUM_26

// Global variables
int canSendInterval = 25;
int lastCanSendTime = 0;
TaskHandle_t CAN_Task;

// Subsystem enumeration
enum Subsystem {
  CVT,
  DASHBOARD,
  DAS,
  WHEEL_SPEED,
  PEDALS,
  BASE_STATION
};

Subsystem currentSubsystem;

// CAN IDs
const int primaryRPM_ID = 0x01;
const int secondaryRPM_ID = 0x02;
const int primaryTemperature_ID = 0x03;
const int secondaryTemperature_ID = 0x04;
const int beltTemperature_ID = 0x05;
const int frontLeftWheelSpeed_ID = 0x0B;
const int frontRightWheelSpeed_ID = 0x0C;
const int rearLeftWheelSpeed_ID = 0x0D;
const int rearRightWheelSpeed_ID = 0x0E;
const int frontLeftWheelState_ID = 0x0F;
const int frontRightWheelState_ID = 0x10;
const int rearLeftWheelState_ID = 0x11;
const int rearRightWheelState_ID = 0x12;
const int gasPedalPercentage_ID = 0x15;
const int brakePedalPercentage_ID = 0x16;
const int frontBrakePressure_ID = 0x17;
const int rearBrakePressure_ID = 0x18;
const int frontLeftDisplacement_ID = 0x1F;
const int frontRightDisplacement_ID = 0x20;
const int rearLeftDisplacement_ID = 0x21;
const int rearRightDisplacement_ID = 0x22;
const int accelerationX_ID = 0x29;
const int accelerationY_ID = 0x2A;
const int accelerationZ_ID = 0x2B;
const int gyroscopeRoll_ID = 0x2C;
const int gyroscopePitch_ID = 0x2D;
const int gyroscopeYaw_ID = 0x2E;
const int gpsLatitude_ID = 0x2F;
const int gpsLongitude_ID = 0x30;
const int gpsTimeHour_ID = 0x31;
const int gpsTimeMinute_ID = 0x32;
const int gpsTimeSecond_ID = 0x33;
const int gpsDateMonth_ID = 0x34;
const int gpsDateDay_ID = 0x35;
const int gpsDateYear_ID = 0x36;
const int gpsAltitude_ID = 0x37;
const int gpsHeading_ID = 0x38;
const int gpsVelocity_ID = 0x39;
const int batteryPercentage_ID = 0x3A;
const int sdLoggingActive_ID = 0x42;
const int dataScreenshotFlag_ID = 0x43;
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

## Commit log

2023-10-15 Update and rename CVT Infrared Sensors Full Model.step to 3D Models / CVT Infrared Sensors Full Model.step
    [CVT Infrared Sensors Full Model.step]
2023-12-02 12/2
    Fixed issues causing build to fail.
    Still need to test.
    [MicrocontrollerSoftware.ino]
2024-03-13 Update and rename 3D Models/CVT Infrared Sensor Mounts.step to 3D Models/OldDesigns/CVT Infrared Sensor Mounts.step
    [CVT Infrared Sensor Mounts.step]
2024-03-13 Update and rename 3D Models/CVT Infrared Sensors Full Model.step to 3D Models/OldDesigns/CVT Infrared Sensors Full Model.step
    [CVT Infrared Sensors Full Model.step]
2024-03-13 Rename 3D Models/CVT Infrared Sensors Main Body (No Temperature Sensor).stl to 3D Models/OldDesigns/CVT Infrared Sensors Main Body (No Temperature Sensor).stl
    [CVT Infrared Sensors Main Body (No Temperature Sensor).stl]
2024-03-13 Rename 3D Models/CVT Infrared Sensors Main Body (With Temperature Sensor).stl to 3D Models/OldDesigns/CVT Infrared Sensors Main Body (With Temperature Sensor).stl
    [CVT Infrared Sensors Main Body (With Temperature Sensor).stl]
2024-03-13 Rename 3D Models/CVT Infrared Sensors Nut.stl to 3D Models/OldDesigns/CVT Infrared Sensors Nut.stl
    [CVT Infrared Sensors Nut.stl]
2024-03-13 Update and rename 3D Models/Sensor Mount No Temperature.step to 3D Models/OldDesigns/Sensor Mount No Temperature.step
    [Sensor Mount No Temperature.step]
2024-03-13 Update and rename 3D Models/Sensor Mount with Temperature.step to 3D Models/OldDesigns/Sensor Mount with Temperature.step
    [Sensor Mount with Temperature.step]
2024-05-14 moving 2023-2024 files to archive
    [CVT Infrared Sensor (no temperature).step, CVT Infrared Sensor Mounts.step, CVT Infrared Sensors (with temperature).step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]
2024-09-19 Major overhaul to program
    Add dynamically adjusting thresholds based on min/max readings
    Replace single midpoint threshold with lower 1/3 and upper 1/3 threshold for more reliable readings
    Modify Serial Prints to work with Plotter
    NOTE: averaging should be used with a timeout for smoother readings
    [MainCode.ino, printData.ino, updateRPMs.ino]
2024-10-18 Update debug prints and add RPM zeroing timeout
2024-11-14 Rename 3D Models/CVTMain v2.step to 3D Models/Alternative Designs/CVTMain v2.step
    [CVTMain v2.step]
2024-11-15 Update Enclosure Model
2024-11-17 Update Enclosure
2024-11-21 Various changes to PCB design
    Changes:
    Move 4 pin aviation plug connector to bottom of PCB
    Move 0.1uF bypass capacitors from Vout to Vs
    Remove voltage divider on TMP36 output. TMP36 output ranges from 0.1V to 2.0V, which is within our 0-3.3V reading range on ESP32
    Change signal voltage divider for IR receiver from 1W footprint to 1/4W footprint
    Combine +5V and GND pads for IR and TMP36
    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
    [CVTPCB.kicad_pcb, CVTPCB.kicad_sch]
2024-11-21 Fix missing silkscreen and flipped orientation of pot
    [CVTPCB.kicad_pcb]
2024-11-21 Fix reversed silkscreen markings
    [CVTPCB.kicad_pcb]
2024-11-21 probably finish sensor pcb
    [SensorPCB.kicad_pcb, SensorPCB.kicad_sch]
2024-11-23 Update PCB to have JST on Back side and add DRL Files
    [SensorPCB.kicad_pcb]
2024-11-24 Fix issue where plane was extending beyond cut line
2024-12-05 Partial fix for incorrect voltage divider
    [CVTPCB.kicad_pcb, CVTPCB.kicad_sch]
2024-12-05 Complete pot/resistor issue fix
    [CVTPCB-B_Cu.gbr, CVTPCB-B_Mask.gbr, CVTPCB-B_Paste.gbr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]
2024-12-05 Update enclosure to work with new PCB design fix
2024-12-07 Remove old GBR/DRL Files
    [CVTPCB-B_Cu.gbr, CVTPCB-B_Mask.gbr, CVTPCB-B_Paste.gbr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]
2024-12-27 Add warning about analog inputs exceeding 3.3V
2024-12-29 Update 3D Models
    [CVT Sensor Module Enclosures v5.step, CVT Sensor Module Enclosures.f3z]
2025-01-06 Fix issue where watchdog being triggered on core 0
    This issue seemed to stem from the size of the stack for the task. It was set to 10000, and I set it down to 1000. This cause guru meditation errors with stack overflow, so I bumped it back up to 2000 and it seems to be working fine now. Also had a concern where analog reads appeared to be taking up to 20ms, but this may have been due to the Serial.prints taking up time. Commenting out all of the printData print messages made the analog reads instantaneous (at least from the perspective of printing the before and after millis() )
    [CVT-Tachometer.ino, printData.ino]
2025-01-07 Add "Ignore Readings" Code
    This code is meant to ignore any calculations that may happen after a long task, such as printing to the serial monitor or sending CAN data. Since we are not actively monitoring the analog reads duri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
2025-01-07 Implement Several Bug Fixes
    Fix issue where packetId was not checked during RTR reception
    Increase baud rate to fix any issues associated with serial prints
    Remove statusCVT print from general sendCAN function; this should only occur upon request
    [CVT-Tachometer.ino]
2025-01-07 Remove serial print from RTR send
2025-01-08 Change temperature status conditions
2025-01-10 Fix bug in readSecondary where if else statements were not executing correctly
    [CVT-Tachometer.ino]
2025-02-12 Temporary Fix for data not updating
    I set the ignoreReadings to false because my hand can only go so fast. However, this presents another issue for the car. If we are only getting something like three revolutions per second, we will never do the math to update because we are sending CAN data 10 times per second. Need to find a solution for this
    [CVT-Tachometer.ino]
2025-02-15 Remove ignore reading code
    Although the serial printing takes ~7000us, it is not worth having ignore reading code. If the readings are too slow (fewer readings per second than instances of printing to serial monitor), then we will never do calculations. The serial printing will not be in place in the final version, so it will have no effect on final accuracy. The CAN sending is nearly instantaneous compared to serial printing, so we do not have to worry about that too much
    [CVT-Tachometer.ino]
2025-02-15 Decrease stability delay, not sure if necessary
    [CVT-Tachometer.ino]
2025-02-15 Put delay back to 1ms because of watchdog timer
2025-03-29 Add small calibration offset to primary temperature sensor
    It reads 65 degrees in a room that is 75 degrees. I think this is just because the voltage that the module is getting is slightly lower/higher than it should be, so this accounts for that.
2025-04-02 FIx ESP32JSA1000 prescale register write
    This fix should eliminate the issue where setting the CAN baud rate actually sets it to half that value
    [CVT-Tachometer.ino]
2025-04-02 Maintain serial print speed at 460800
2025-04-12 Fix Noisy Temperature Sensor Readings
    Not entirely successful, but helps noise on temperature sensor readings a bit. Just averages 10 readings before calculating
    [CVT-Tachometer.ino, printData.ino]
2025-05-01 Switch to fixed resistors, increase debug print interval
    [CVT-Tachometer.ino, printData.ino]
2025-05-01 Add delay only when CAN sends to allow watchdog to reset on secondary core
    [CVT-Tachometer.ino]
2025-05-10 Several updates
    I think the status bits / RTRs may have been causing issues, so those are removed.
    In the case that extremely long CAN messages (like sending 250000 RPM) are causing the issues on startup (when the CVT sensors have not been calibrated), I added a statement that first checks if the CVT has calibrated itself. If it has not, it jut sets the RPM value to zero
    [CVT-Tachometer.ino]
2025-05-10 Remove temp prints
2025-05-10 Reduce time between serial prints (see explanation)
    Although keeping the serial print frequency lower helps to have more analog reads, you can't even see what's happening. So for debugging purposes, a higher frequency is slightly less accurate but bet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
2025-05-10 Turn off serial printing
2025-06-14 Fix primary temperature offset
2025-07-05 See description
    Untested code, adds some features for better accuracy when sampling. Now, ADC takes five samples of the IR pin and averages before using primaryValue and secondaryValue in calculations.
    abs was added to the threshold checker. This probably won't make a difference, but makes the code slightly more robust against weird errors and also easier to understand/read
    ignoreNextReading was added to the secondary code. Especially with the new averaging, sending data to the CAN bus and delaying 1ms for the watchdog could be enough to miss or just get the edge of a sensing target. Better safe than sorry, missing one reading is not crucial to data interpretation but having an incorrect o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
    [CVT-Tachometer.ino]
2025-07-25 Several Updates
    Increase number of samples for multisampling
    Added large decoupling caps to power pins
    Added small decoupling caps to analog input pins
    Added exponential growth and decay instead of regular min/max for creating bounds
    Added small microseconds delay between analogreadings for IR when averaging
2025-09-06 Fix printing
2025-09-06 Change CVT temp readings to ints instead of floats. See description
    This float sending doesnt work with the latest 2.0.0 can driver that everything else uses. We really don't need decimal precision anyway, so until tihs subsystem is updated to use all interrupts and 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
2025-09-08 Update to new PCB
    This PCB features comparators with hysteresis added, surface mount hardware for voltage regulation and CAN protocol, and numerous test points for debugging
    [CVTPCB.kicad_pcb, CVTPCB.kicad_sch]
2025-09-27 Update PCB to use comparator, includes new GBR and DRL
    [CVTPCB.kicad_pcb, CVTPCB.kicad_sch]
2025-10-11 (MAJOR) Update CVT program to use comparator readings
    Applicable to '25 car revamped board and will also be used on '26 car
2026-04-26 Add MLX90640 hot spot reading to replace MLX90614 belt temp sensor
